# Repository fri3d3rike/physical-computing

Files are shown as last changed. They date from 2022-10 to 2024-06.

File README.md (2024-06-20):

# Physical Computing SS23 - Group 09

## Who we are

Friederike Mirza

We are Friederike Körte and Mirza Özokyay. Friederike is a Bachelor's student currently starting her advanced studies. Mirza is a Master's student and is familiar with electronics. 

## Topic

We are creating a telepresence system. Our device supports video calls by moving a tablet so that the participants of the call can see each other, even if the local participant moves to the left or right of the device. The device can follow a local participant's face or be manually controlled by a remote participant.

## Repository Structure

| Directory | Purpose |
|---|---|
| `Project` | Everything related to your project. |
| `Project/Concept` | Everything related to the concept or design of your project (ideas, drawings, mockups, mind maps, etc.). |
| `Project/Electronics` | Everything related to the electronics of your project (circuit diagrams, datasheets, etc.). |
| `Project/Mechanical` | Everything related to the mechanical aspect of your project (CAD, blueprints, datasheets, assembly, etc.). |
| `Project/Software` | The software aspect of your project. Most likely source code. |
| `Weekly Reports` | Weekly status updates as Markdown files. |
| `Weekly Reports/Figures` | Pictures or videos for your weekly reports. |

## Weekly Reports

Create a file called `PhysComp SS23 Group 09 Week <NN>.md` for every weekly assigment in `Weekly Reports`. For example: `PhysComp WS23 Group 02 Week 03.md`. Strictly follow this naming scheme and do not change it!
If you include pictures of videos, put them in `Weekly Reports/Figures`.

## Repository

### LFS

This template already comes with a pre-defined configuration for [Git LFS](https://git-lfs.github.com/). If you add any large binary files to your repository, update `.gitattributes` accordingly using `git lfs track`. For example if you add other video formats or CAD files that are binary, you need to track their file extension.

### .gitgnore

Please create according `.gitignore` files to ignore unnecessary files in the repository such as temporary files or build artifacts.

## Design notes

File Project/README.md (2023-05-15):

# PhysComp SS23 - Telepresence System

We are working on a device that holds a tablet and follows the user's face during a video call. The device can also be manually controlled by a remote participant. There are three operating modes: Stand (do nothing), Follow (the local participant's face) and Manual (controlled by remote user). The mode can be selected locally via a button on the device. The button is illuminated to show which mode is selected. Below the device, there is a sublte indirect light indicating the remote connection status (green/red). The device automatically powers on when a tablet is placed into the holder.

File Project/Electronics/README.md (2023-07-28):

# Electronics

The LEDs are connected to the Raspberry Pi GPIO pins with appropriate 220 Ohms resistors. The buttons are also connected to GPIO pins with configured pull-ups.

The connections of the ultrasonic sensors are interesting:

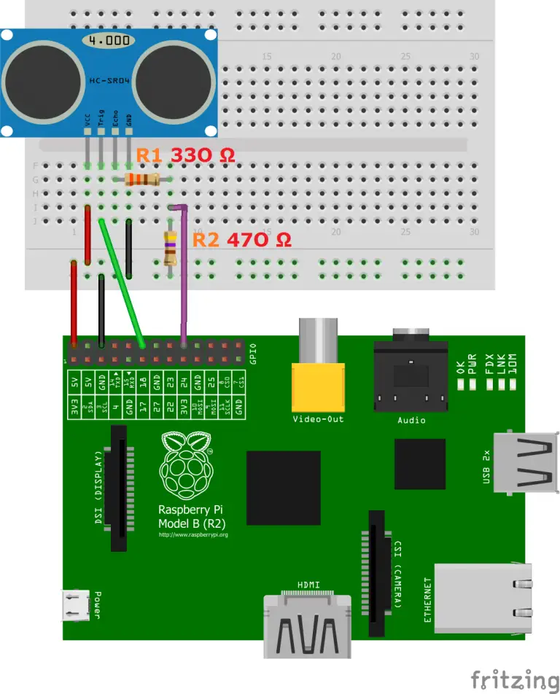
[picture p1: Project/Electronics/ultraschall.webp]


Source: https://tutorials-raspberrypi.de/entfernung-messen-mit-ultraschallsensor-hc-sr04/

We changed the 470 Ohms resistor to a 10k Ohms resistors which is said to work better.

The rest is described in the project reports, which is also where you can find our component list.

We wired everything on a breadboard.

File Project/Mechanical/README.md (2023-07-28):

# Mechanical

We create no sophisticated mechanical mechanism. The tablet angle can be chosen and of course the omni wheel platform enables the devices to drive around. Sketches, drawings and CAD files are in our concept folder.

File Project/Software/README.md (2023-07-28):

# Software

We wrote software to control the functionality of our prototype. There are two processors that we programmed:

* The Arduino Uno is for controlling the motors
* The Raspberry Pi is for handling user input and sending signals to the Arduino

## Arduino

The Arduino program is written in C and uses the Adafruit Motor Shield Library V2 to control the motors via the shield mounted onto the Arduino. It receives serial commands via USB from the Raspberry Pi. These commands contain (one byte each):

* Axis (forward/backward, left/right, rotate)
* Direction
* Motor speed

The program reads the serial commands in a loop and then sets the motor speeds accordingly. It also balances the speeds because one motor is weaker than the others. The progrma can be uploaded run from any Arduino compatible IDE.

https://github.com/adafruit/Adafruit_Motor_Shield_V2_Library

## Raspberry Pi

The Raspberry Pi is the brain of our prototype. It runs the latest Raspberry Pi OS Lite. Initially, we chose the Raspberry Pi because it is capable of image processing for the tracking mode. But since the actual tracking was not a top priority, we never actually implemented it. The main reason for that is that for some reason, the OpenCV library would not load the required modules. The Raspberry Pi handles all user input and sends commands to the Arduino. We simulated functionality that is not implemented via SSH. The Raspberry Pi does the following:

### A web server that serves our web UI

Since the Raspberry Pi has WiFi, we can connect it to a router and then access a small web server on it. The web server is realized in with Flask in Python. You can start it via ``start.sh``. It serves a static HTML page that has JavaScript code for GET requests when a button or key is pressed, found in ``static/index.html``. The GET requests are then handled by the Raspberry Pi. If the device is not in freeze mode, then the commands are forwarded to the Arduino to control the motors via serial commands. Since the hostname ``raspberrypi.local`` didn't work reliably (often quite delayed), we set up a static LAN address in the router.

Our code for the serial communication ``control.py`` was inspired by https://tutorials-raspberrypi.de/arduino-raspberry-pi-miteinander-kommunizieren-lassen/. We had to alter it to work with the current version of the library. 

### A Python script for our front panel

The ``frontpanel.py`` controls our front panel logic. It polls the buttons and sets the LEDs accordingly if a button is pressed. It also creates or removes the freeze file which indicates whether remote control has any effect. Since the "follow" mode is not implemented, it behaves the same as the "remote" mode, so we can simulate it.

### Some bash scripts for simulating functionality

The scripts ``red.sh``, ``green.sh`` and ``off.sh`` control the status LEDs below the device. Sine we have no actual login or connection system for the web UI, this simulates updating the status LEDs due to a user connecting/disconnecting.

### A python program for testing the ultrasonic sensors

The scripts ``ultra.py`` and ``ultra2.py`` poll from the left/right ultrasonic sensors. They show that the sensors are able to consistently detect edges. However, the data was never used because we did not want to risk our prototype breaking. Low motor speeds were not possible due to the weight, so the device was always a bit fast.

We took the electronic circuit and code from https://tutorials-raspberrypi.de/entfernung-messen-mit-ultraschallsensor-hc-sr04/ (modified).

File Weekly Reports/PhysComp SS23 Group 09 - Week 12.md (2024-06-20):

# PhysComp SS23 Group 09 - Week 12

## Progress Report

### What we achieved this week

We made our prototype ready for the evaluation. Here is a list of what we have accomplished:

* Added front panel button labels
* Created web interface for remote-controlled driving
* We tested a direct connection to a laptop using a self-hosted WLAN hotspot
* The connection was too unstable, so instead, we used a WLAN router for relaying the requests
* Tested the driving, found out that the batteries were too weak and replaced them
* Compensated a slow motor that caused the device to always turn by reducing the power of the other motors
* Added status LEDs below the device
* Added the on-off switch that is activated by placing the tablet into its slot
* Implemented logic for simulating the on-off switch (turns LEDs and functionality on/off)
* Implemented front panel logic (mode selection, corresponding LED is on, device ignores move commands if in freeze mode)
* Implemented a way to remote-control the status LEDs (red/green) below the device
* Glued on a power bank holder and the front panel

For photos, we refer to the evaluation.

We reached milestone 4 and part of milestone 5.

### What we could not achieve this week

We have not mounted the ultrasonic sensors and camera. This was not a problem because we had already planned to fake the edge detection and people recognition.

### What we plan to do for the coming week

* Mount the ultrasonic sensors and camera
* Incorporate some of the feedback from the evaluation: slower driving speed/acceleration, better web user interface
* Implement some way of detecting a connected remote user so that we don't have to fake it
* Maybe more improvements if there is time
* Reach milestone 5
* Send refund requests for the components we bought

## Evaluation Report

### Participants

We recruited our six participants from students of other courses. For that, we asked them personally or wrote them texts on WhatsApp. Students are a good representation of our target group because after the pandemic, they are very familiar with video calls and the problems that can arise. We recruited them between the 4th and 7th of July 2023.

All participants signed letters of consent and agreed on being recorded for our evaluation.

We had three groups of two participants each. One participant participated in the meeting in a room with Friederike using our device. The other participant went to a different room with Mirza.

### Functionality

The mode selection with LED feedback was actually working (except for the follow mode as mentioned before). In the freeze mode, no remote control is possible. Also, the remote-controlled driving was real since it is our core functionality.

We faked a lot of functionality. Since our web interface does not have a password-protected login system, remote users do not actually keep a connection to the device. They just send requests whenever they issue a drive command. This is why Mirza simulated the connection status LEDs (red/green/off) by remotely running commands on his laptop at the correct times. We also faked the automatic following mode since it was not ready. Mirza remote-controlled the device from his laptop in this mode. We did not find a safe way to fake the edge detection, but we made sure that the situation would not arise by starting the experiment with the device in the middle of the table. This was important to protect the device from damage. We also faked the on-off switch. The effects were basically the same as if it were actually implemented (LEDs turn on/off, the device does not respond to commands when off, the device always starts in freeze mode). The only difference was that the power to the Arduino and Raspberry Pi was kept on, allowing us to always be able to intervene if something were to go wrong. Also, this was much easier to implement instead of actually hooking up all the components to the switch.

### Instructions

We changed some of the tasks to be more focused on the core concept and capabilities of our device.

- **Task 0: Splitting up:**
  One user (local) stays with Friederike and the device. The other one (remote) goes to another room with Mirza.

- **Task 1: Device Setup:**
  The local user is provided with a tablet which is already in a Zoom call with Mirza's laptop next door. The remote participant can hear the instructions for the local participant through the call. The local participant is asked to turn on the device by placing the tablet in the holder.
  While doing that we observe the user's experience during the setup process, noting any difficulties or confusion encountered.

- **Task 2: Switch Device into the Remote Mode:**
  The user with the device is asked to switch from the default mode of the device into the Remote Mode. Then the user is asked to check the connection status of the device (simulation by Mirza).

- **Task 3: Remote Control:**
  The remote user is asked to move the device manually to look at Friederike who sits outside of his field of view next to the local participant.
  We observe if the device successfully moves and rotates toward Friederike. We check if it draws attention due to excessive noise, delays, or inaccurate movement.
  We observe if the remote user can interact with the user interface. We instruct them to also try out the control via the arrow keys instead of the buttons.

- **Task 4: Follow Mode Selection and Rotating Functionality:**
  The local user is asked to select a mode that causes the device to automatically follow a person in front of it. They are encouraged to move around so that the device has to rotate to keep them in the video.
  We observe if the device successfully rotates according to the user's input (simulated).

- **Task 5: Freeze Mode selection:**
  The users are instructed to set a mode that stops the device from moving and prevents remote control. We encourage the remote user to attempt to move the device.
  We observe if the mode selection is intuitive.

- **Task 6: Turn off the device:**
  The local user is asked to turn off the device. If they do not know how, we give them the hint to take away the tablet.

### Observations

We made many interesting observations when watching the participants interact with our prototype.

* Although we explained the concept of our speak-aloud study, the participants generally kept quiet. We had to ask them to comment on their observations.
* If the tablet is in a protective case, some force is needed to push it into its place and activate the power switch. The first participant was not sure if they should apply so much force. For later trials, we removed the tablet case, making the process much simpler.
* One local user placed the tablet in portrait orientation instead of landscape orientation. We instructed them to change to landscape so that the tablet would not fall over.
* During one trial, a wheel came off. We were able to quickly stick it back onto its axle and continue the experiment.
* One participant acted as if they were afraid that the device could drive off the table.
* To one participant, it was not clear that the front panel LEDs are pushable buttons.
* During movement in one trial, the tablet briefly came off the switch, causing the device to quickly turn "off" and reset to the freeze mode. This was very unexpected and confused all of us.
* Some local participants did not notice the status LEDs below the device. We believe that this is because especially the red LEDs are not bright enough.
* In our web interface, users often did not use the "turn left"/"turn right" buttons, but instead only the "left" and "right" buttons. We should probably swap their places to make the more important rotation buttons more prominent. Likewise, the left/right arrow keys should control the rotation and only need "shift" for driving sideways.

Here are some pictures of us doing the evaluation with the participants:

At the beginning:

Evaluation

Our participants filling out the survey (Google Forms):

Evaluation

A remote participant in the other room:

Evaluation

One study participant while testing the rotating functionality:

<video src="Figures/evaluation.mp4" controls width="100%"></video>

### Online Surveys

Both participants answered the same surveys. Some questions were more suitable for either the present or remote participant, but we always let both answer all questions from their perspectives. We evaluate them separately if appropriate.

#### Pre-Test Survey

Pre-Test Survey
Pre-Test Survey
Pre-Test Survey
Pre-Test Survey
Pre-Test Survey
Pre-Test Survey
Pre-Test Survey
Pre-Test Survey
Pre-Test Survey

Participants generally understand the idea of a telepresence device (some needed a short explanation during the survey). They saw a need for such devices. Many were not very familiar with telepresence devices, though. Also, more than half of our participants were not confident with controlling a physical device via web-based interface.

#### Post-Test Survey

Post-Test Survey
Post-Test Survey
Post-Test Survey

Was the mode selection intuitive?  
$\Rightarrow$  all participants answered with highly intuitive

How intuitive and user-friendly did you find the mobile app or web-based interface for controlling the device?  
$\Rightarrow$  all participants using the interface answered with highly intuitive

Post-Test Survey
Post-Test Survey
Post-Test Survey
Post-Test Survey
Post-Test Survey

Our participants found the setup easy. They liked the (simulated) automatic tracking. All participants agreed on the mode selection being intuitive. They all found the web interface to be highly intuitive. Participants criticized that the device was a bit unstable/unsecure. Participants were mostly comfortable during the session, but this did not apply to all.

They gave us helpful feedback regarding a free space for the device and suitable ground and also pointed out that there would be fewer problems if the device only rotates. This is nothing really new to us, but it shows us that they understood the concept very well.

Our participants suggested refining the movement behavior (less stuttering and noisy). They would like obstacle/edge detection and a more secure tablet holder that also secures the tablet on the sides.

All except for one would use the device. One participant thinks that the device is overkill for small meetings.

### Post-Test Interview

After the experiment and the post-test survey, we briefly interviewed our participants together in person. We chose to do it this way to make it as comfortable as possible for them. We asked them especially for anything that they would like to comment on but did not write into the survey. We encouraged them to tell us everything about their experience during our study that came to their minds. Here are their comments:

* The device is quite loud
* The device might fall off the table
* The tablet camera angle is not ideal for large tables
* A way to remotely control the tablet angle vertically would help
* The device moves stuttering 
* Unexpected movement scared someone
* The device is probably very good for presenters like professors
* A user placed the tablet in portrait orientation only because it already was this way on the table
* When asked, nobody noticed the possibility to manually change the vertical tablet angle
* A way to secure the tablet on the sides would be good
* Unsure what happens if there are many people in front of the device in automatic following mode
* The device is quite big and does not fit in a small bag, so it is not very portable
* Sometimes, the automatic tracking is too slow (was simulated to be as realistic as possible)
* Participants generally liked our front panel, the button labels, colors, and feedback due to the LEDs lighting up
* At the beginning, it was not clear what the status LEDs below the device communicate (until they turned green exactly when the remote user "connected")

After the study, participants received a Kinder Bueno as compensation for their time.

### Conclusions

We are very happy that our participants liked our core concept. Participants found interaction with parts of the device that were in our main physical concept very intuitive, specifically powering the device on/off by placing/taking the tablet and the mode selection. This is especially good when considering that in the pre-test survey, many participants were not familiar with telepresence devices.

We cannot make fundamental changes to our concept so shortly before the final presentation. For example, we cannot implement remote control for the vertical tablet angle. However, there are small things that we can polish:

* We can reduce the motor speed to make the device less scary, loud, and abrupt
* We can make the acceleration gradual to make movements smoother
* We can swap the "turn" and sideways (left/right) buttons of our web interface
* We can add ultrasonic sensors for edge detection (or at least the simulation of it for our presentation)

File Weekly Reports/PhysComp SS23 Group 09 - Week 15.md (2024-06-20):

# PhysComp SS23 Group 09 - Week 15 - Final Report

## What we achieved in Week 14

As planned in our previous report, we added a third ultrasonic sensor in the back. This way, there is no risk of driving off an edge when going backward. There is no ultrasonic sensor in the front because we found nowhere to put it, it would look stupid and it also is not really necessary since you can see where you are going when driving forward.

Ultrasonic Sensor Back

The ultrasonic sensors on the sides are wired up and working. However, we don't trust them enough to test the edge detection when actually driving. Due to the weight of our device, the motors require a minimum power that makes it go quite fast. The measurements prove that it is indeed possible to detect an edge from the readings in theory.

Ultrasonic Sensor Console

Code by https://tutorials-raspberrypi.de/entfernung-messen-mit-ultraschallsensor-hc-sr04/

We also asked other students whether we should encase the ultrasonic sensors. The voted for yes with 2:1 votes. Our prototype now looks more polished:

Ultrasonic Sensor Exposed
Ultrasonic Sensor Encased

We decided that it isn't worth the effort to do more programming or even try to implement more functionality. Proper tracking would be nice, but also very time-consuming to implement. We fixed a few bugs with the UI, though. In its current state, with a little bit of magic, our prototype can exactly showcase our whole vision for the telepresence system. This is why we call it complete and milestone 5 is reached (almost on time).

### We also found a missing photo of our drawing for the wooden parts

Wood Drawing

We gave this drawing to the scientific engineering services. They cut our wood parts.

### Updated READMEs

We updated the READMEs of all directories in the Project directory to include useful information.

## Concluding report

Our prototype is a Telepresence Device designed for users attending hybrid meetings with their laptop or tablet. Its goal is to achieve a more active engagement in remote meetings.

### What works:
- Turning on the device with a switch by placing the tablet inside the holder
- Selecting between 3 different modes to change between different functionalities of the device
- Giving the user feedback about which mode is currently selected by the according LED light, inside the button that was pressed, being turned on
- The device has red and green status LEDs underneath
- The device does not move when in mode: freeze
- The device moves in response to the remote participant pressing the keyboard or interacting with the graphical interface (and that pretty well and accurately)
- There is a graphical interface with which the remote participant can control the device
- The device has two out of three wired and working ultrasonic sensors to detect edges

### What plans changed:
- We found a camera for the Raspberry Pi and then changed the concept to have a more independent device which does not also have to access the connected tablet/smartphone's camera
- We didn't fully implement the edge detection because we already planned in the beginning that that is not our main focus and we would only do it in the end, if we have enough time (optional goal)

### What doesn't work:
- The tracking functionality (the OpenCV library caused problems)
- The feedback whether there is a connection to a remote (red/green status LEDs) user is not automatic yet (there is no login system)
- The edge detection: The ultrasonic sensors on the sides are wired up and working, only the one on the back is not wired. They do not force the device to stop yet if an edge is detected. We did not implement it because we would not risk our device being damaged anyway.

### What could work if...:
- All the things that are not completely functional yet could be improved to work if we would have had more time
- The ultrasonic sensors, as well as the feedback LEDs, are connected to the Raspberry Pi, they just need to be implemented in the code to fully work (use the sensor readings which we already have, create some kind of session in JavaScript for the LEDs)
- The tracking would be a little bit more effort than the other things, but the camera is already connected and works and communicates with the Pi, so we would need to get the library working. Then just send the appropriate motor commands if a face is detected far enough off-center.
- If the device were a bit lighter, then the motors could go slower (yes, it's counter-intuitive). After the evaluation, we reduced the speed, but an even slower speed might be desirable.

### Demonstration

You can access our final presentation as [PDF](../Project/Concept/PhysComp_SS23_Final_Presentation.pdf) and [PPTX](../Project/Concept/PhysComp_SS23_Group_09_Final_Presentation.pptx) (with some videos included).

Here are all videos to show the prototype in action (please ignore the beeping sounds of our neighbor's prototype):

##### Setup 


##### Mode Selection


##### Remote Modus: UseCase 1


##### Tracking Modus: UseCase 2


##### Edge Detection  


##### Device Rotating  


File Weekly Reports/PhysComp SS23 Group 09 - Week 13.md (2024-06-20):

# PhysComp SS23 Group 09 - Week 13

## Progress Report

### What we achieved this week

We implemented all of the missing hardware features and improved our software.

* Mounted the camera module, connected it to the Pi
* Added ultrasonic sensors, they are wired up and give measurements
* Added cardboard brackets that hold the tablet in place
* Changed the resistors for our red status LEDs from 220 Ohms to 120 Ohms to make them brighter
* Improved the web UI: swapped the buttons/keys for turning and strafing

#### New web UI
The web UI

#### Final state of the electronics underneath the hood
Electronics
Electronics

#### Final state of the prototype
Final Prototype
Final Prototype with Tablet

<video src="Figures/prototype_moving.mp4" controls width="100%"></video>

### What we could not achieve this week

We haven't added four ultrasonic sensors, only two.

### What we plan to do for the coming week

* Maybe add another two ultrasonic sensors, if we can find a way to mount them. Then all movement directions are safe.
* Maybe implement an easier way of simulating the webUI authentication and connection for the status LEDs
* Prepare and exercise our presentation

## Evaluation Report

There was nothing new to evaluate.

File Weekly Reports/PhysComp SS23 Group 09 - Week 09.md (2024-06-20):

# PhysComp SS23 Group 09 - Week 09

## Progress Report

### What we achieved this week

#### Arduino Motor Test
We decided that it is easiest to use the motor shield with our Arduino since it is designed to work with it. We still need the Raspberry Pi for the image processing, though. So our project will use both an Arduino and a Raspberry Pi.

We mounted the motor shield onto the Arduino. This was easy, because we had desoldered many unnecessary wires a few weeks prior. A problem was that a poorly soldered pin had a connection issue, but with some pushing and pulling, it is solved for now. We might want to re-solder the pin if the problem arises again. We then ran the example code for the motor shield as a test.

Motor Test

#### Raspberry Pi
In order to get the Raspberry Pi working, we borrowed an SD reader from another group (we expected the Uni to have a microSD-SD adapter, but there was none to be found). We then installed a Raspbian Lite image onto our microSD card and configured it to connect to my laptop via WLAN. After a bit of troubleshooting, everything worked fine. We then tried connecting the Raspberry Pi to the Arduino via USB, but there seems to be some issue with the serial port configuration on the Pi. We have to look into that next week.

We also decided to use the Raspberry Pi camera module which we found in a box in the HCI lab. This way, our system can operate independently from the tablet, making it much simpler and hopefully more robust. We have to figure out where to mount the camera.

#### Building the Physical Parts
We created plans with proper measurements for the base that connects the tablet holder to the omni wheel platform. Unfortunately, we forgot to take pictures. We gave the plans and some wood scrap to the engineering services and hope to receive our parts in the next few weeks.

We also 3D printed our front panel. It came out exactly as expected.

Front Panel Printed
Front Panel Printed

### What we could not achieve this week

* Construction plan for the top part (including spot for the Raspberry Pi camera)
* Plan for mounting the ultrasonic sensor
* Raspberry Pi to Arduino connection

### What we plan to do for the coming week

* Plan the top part, camera, and ultrasonic sensor placement (reach Milestone 1)
* Hopefully receive parts from the engineering services, work on the top part (toward Milestone 2)
* Connect Raspberry Pi to Arduino for motor controls, test the camera (toward Milestone 3)

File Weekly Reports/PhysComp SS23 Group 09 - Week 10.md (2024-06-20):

# PhysComp SS23 Group 09 - Week 10

## Progress Report

### What we achieved this week
Friederike could not attend the lecture due to the overlap with another course, but worked from home. 
We got the wood parts we had ordered at the wood workshop and prepared them for the next milestone.

Wood Parts
Wood Component

We also managed to get the connection from the Raspberry Pi to the Arduino to work. We had to replace the camera cable to connect the camera to the Pi. For that, we borrowed a high-quality camera module with a compatible cable. We do not use the high-quality camera module, because it is very big and also requires a big lens which we do not have. With the new cable, our camera works, but for some reason, the OpenCV library does not load certain modules on the Pi. We might implement the face tracking in a Wizard of Oz fashion.

The first photo taken with the Raspberry Pi camera:

First Pi Cam Image

### What we could not achieve this week

The OpenCV library does not load the modules required for the face tracking. Also, the LEDs still have to be connected and the front panel must be assembled. The LED and motor controls have to be programmed.

### What we plan to do for the coming week

* Reach milestone 3
* Assemble everything (top part of the device, front panel, LEDs, camera, on-off switch)
* Set up the remote control

## Evaluation Plan:

### Usability Test Plan: Telepresence Device for Hybrid Meetings

### Introduction:
The purpose of this usability test is to evaluate the functionality, ease of use, and overall user experience of the telepresence device designed for users attending hybrid meetings. The target group for this test is people who actively engage in remote meetings and need a seamless and immersive experience. The test will focus on assessing the device's rotation capabilities, tablet/phone holding mechanism, setup process, adaptability to different meeting spaces, and user interface.

### Test Objectives:

- Evaluate the ease of setup and use of the telepresence device (turning it on).
- Evaluate the ease and understandability of the mode selection.
- Assess the functionality of the device's ability to rotate and its ability to follow a person's face.
- Determine the effectiveness and security of the tablet/phone holder.
- Test the adaptability of the device to different meeting spaces.
- Evaluate the intuitiveness and user-friendliness of the web-based interface of the remote participant.
- Gather feedback on overall user experience and identify areas for improvement.

### Number of Test Users:
To test the device we need at least pairs of two. So that one person can be with the physical product while the other person interacts remotely (ideally from another room). If possible, it is preferable to have even multiple users interacting simultaneously during the test to simulate realistic meeting scenarios and assess any potential issues with concurrent usage.

### Target Group:
Users who regularly participate in hybrid meetings with their tablet/pc/smartphone etc. and require remote participation. The participants should have experience with remote collaboration tools and video conferencing software like Zoom, Teams, etc. Students are an ideal test group since they have experienced lots of video calls during the pandemic. They know the problems that they have had and can understand how they would benefit from our device.

### Test Tasks and Scenarios:

- **Task 1: Device Setup:**  
  The user with the device is asked to unpack and set up the telepresence device on a table or desk. The user is provided with a tablet and asked to turn on the device by placing the tablet in the holder.
  While doing that we observe the user's experience during the setup process, noting any difficulties or confusion encountered.

- **Task 2: User Interface:**  
  The users are provided with a web-based interface for controlling and connecting the device.
  Then both of the users are instructed to connect to the device using the interface.
  We observe the user's interactions and note any challenges or areas of confusion. Do the two groups get the device to connect without problems?

- **Task 3: Remote Control:**  
  The remote user who is not present in the room with the device is asked to rotate the device manually to look at different participants in the other room.
  We observe if the device successfully rotates to track the user's face and adjusts its position accordingly. Drawing attention to excessive noise, delays, or inaccurate tracking.

- **Task 4: Mode selection:**  
  The users are instructed to set the mode to the freeze mode to prevent remote control. Then they are asked to select a mode that causes the device to automatically follow a person in front of it.

- **Task 5: Rotating Functionality:**  
  We instruct the user with the device to move around in the room while the device is set to follow their movements.
  We observe if the device successfully rotates according to the user's input and if the control via the keyboard was intuitive.

### Test Procedure:

1. **Introduction and Pre-Test Survey:**  
   Providing an overview of the test objectives and procedures to the participants. Asking for permission to collect the data and informing them what the data is needed for. 
   Collecting background information about the participants, including their experience with hybrid meetings and remote collaboration tools.

2. **Demonstration:**  
   We present a brief demonstration of the telepresence device's features and capabilities to familiarize participants with its functionality.

3. **Test Execution:**  
   We encourage the participants to think aloud, express their thoughts, and verbalize their experiences as they use the device.
   Assigning the tasks to the participant and taking notes on participants' interactions, difficulties, and feedback.

4. **Post-Test Survey:**  
   Post-test questionnaire to gather additional feedback and subjective impressions from the participants.
   Participants can ask questions, share their overall impressions, and provide any additional comments.

### Additional evaluation technique: Survey 

#### Pre-Test Survey: 

1. How frequently do you participate in hybrid meetings or remote collaborations? - [never, monthly, weekly, daily]
2. Which tools or devices do you currently use for remote meetings? Please rate their effectiveness on a scale of 1 to 5. [1 - Not effective, 5 - Highly effective]
3. On a scale of 1 to 5, how challenging do you find it to actively engage in remote meetings? [1 - Not challenging, 5 - Highly challenging]
4. How familiar are you with telepresence devices or similar technologies? Please rate your familiarity on a scale of 1 to 5. [1 - Not familiar, 5 - Very familiar]
5. On a scale of 1 to 5, how important is it for you to actively engage and contribute during remote meetings? [1 - Not important, 5 - Very important]
6. Have you used any rotating or tracking devices before? Please rate your experience with them on a scale of 1 to 5. [1 - Negative experience, 5 - Positive experience]
7. How confident are you with using mobile apps or web-based interfaces for controlling physical devices? Please rate your level of confidence on a scale of 1 to 5. [1 - Not confident, 5 - Very confident]
8. What features or functionalities do you expect from a telepresence device for hybrid meetings?

#### Post-Test Survey:

On a scale of 1 to 5...

1. How would you rate the ease of setup and initial configuration of the telepresence device? [1 - Very difficult, 5 - Very easy]
2. Did you find the rotation functionality of the device effective in tracking your movements? [1 - Not effective, 5 - Highly effective]
3. Was the mode selection intuitive? [1 - Not intuitive, 5 - Very intuitive]
4. Did you feel that the telepresence device enhanced your ability to actively engage in the hybrid meeting? [1 - No impact, 5 - Significant impact]
5. On a scale of 1 to 5, how intuitive and user-friendly did you find the mobile app or web-based interface for controlling the device? [1 - Not intuitive, 5 - Highly intuitive]
6. How secure and stable did you find the tablet/phone holder for different sizes of devices?  [1 - Not stable, 5 - Highly stable]
7. How comfortable did you feel using the telepresence device during the test session? [1 - Not comfortable, 5 - Very comfortable]
8. Were there any challenges or difficulties you encountered when adapting the device to different meeting spaces?
9. What suggestions do you have for improving the overall usability and functionality of the telepresence device?
10. Based on your experience, would you consider using the telepresence device for your future hybrid meetings? Why or why not?

### What we hope to learn 

* What are common issues, patterns, and areas of improvement?
* Do people understand how to use the device (setup, mode selection)?
* What could be specified more clearly?
* How would we create a manual for the device?
* Are there any risks when using the device?

### What functionality can you test, what can you fake (Wizard of Oz)?

The changes in LED lights in response to button presses (mode selection, on/off switch, connectivity light) are hard to fake but easy to actually implement. We might have to simulate the device detecting edges via the ultrasonic sensors. Also, we might have to fake the mode of following a person if we cannot get the OpenCV library to work on the Pi.

Gif

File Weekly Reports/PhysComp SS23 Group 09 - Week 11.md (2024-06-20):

# PhysComp SS23 Group 09 - Week 11

## Progress Report

### What we achieved this week

Soldering
Soldering

We worked on Milestone 4. We soldered the buttons and connected them to the front panel. 

Frontpanel

We assembled all the inner parts and started programming.

Inner Parts
All Together

In theory, the functions for moving in different directions are now ready, but we have not tested them.

We also created the labels for the front panel:

Front Panel Labels

We created a letter of consent: [consentletter.pdf](/Project/Evaluation/consentletter.pdf)

We also created two Google Forms for the pre and post test surveys and a consent form for our Evaluation Plan.

### Concept Change

Since we are using the Raspberry Pi camera for tracking participants, we no longer rely on a connection to the tablet. This makes our device more robust and makes the setup even easier. Now, the status LEDs no longer display the connection to the tablet, but:
- If the mode is freeze: whether the device is on
- If the mode is follow: whether the device is detecting a participant to follow
- If the mode is remote: whether a remote user is connected

### What we could not achieve this week

* Find people for the evaluation
* Milestone 4

### What we plan to do for the coming week

Finish milestone 4 and start with 5:
* Front panel button labels
* Test driving
* Create web-interface for movement control
* Add status LEDs below the device
* Add on/off switch
* Write logic for controlling LEDs and on/off switch
* Assemble the rest (front panel, power bank, tablet holder)
* Low priority: Mount ultrasonic sensors and camera (not used for evaluation)

Find people for the evaluation of our prototype and evaluate.

## Evaluation Plan Refinement

For the Evaluation Plan, most remained the same as you can find in the last report of week 10. We added the handout of a consent form in the introduction step of the procedure and also reworked the test tasks a little bit to be more specific.

### Introduction:
We greet the participant, introduce ourselves, and briefly describe our project and the purpose of this study:
The purpose of this usability test is to evaluate the functionality, ease of use, and overall user experience of the telepresence device designed for users attending hybrid meetings as part of the Physical Computing Course SS23 at the University of Konstanz. The target group for this test is people who actively engage in remote meetings and need a seamless and immersive experience. The test will focus on assessing the device's rotation capabilities, tablet/phone holding mechanism, setup process, adaptability to different meeting spaces, and user interface.  
Then we give the participant a consent form to sign and introduce them to the tasks. 

### Test Tasks and Scenarios:

- **Task 1: Device Setup:**   
  The user with the device is asked to unpack and set up the telepresence device on a table or desk. The user is provided with a tablet and asked to turn on the device by placing the tablet in the holder. Then both of the users are instructed to connect to the device.
  While doing that we observe the user's experience during the setup process, noting any difficulties or confusion encountered.

- **Task 2: Switch device into the Remote Mode:**  
  The user with the device is asked to switch from the default mode of the device into the Remote Mode. Then the user is asked to check the connection status of the device.

- **Task 3: Start Video Call:**  
  The participants are asked to start a video call.
  We observe how confident the user is with the use of their laptop. 

- **Task 4: User Interface:**  
  The users are provided with a web-based interface for controlling the device.
  We observe the user's interactions and note any challenges or areas of confusion. Do the two groups get the device connected without problems?

- **Task 5: Remote Control:**  
  The remote user who is not present in the room with the device is asked to rotate the device manually to look at different participants/directions in the other room.
  We observe if the device successfully rotates to track the user's face and adjusts its position accordingly, drawing attention to excessive noise, delays, or inaccurate tracking.

- **Task 6: Follow Mode selection and Rotating Functionality:**  
  The users are asked to select a mode that causes the device to automatically follow a person in front of it. They are encouraged to move around.
  We observe if the device successfully rotates according to the user's input and if the control via the keyboard was intuitive. 

- **Task 7: Freeze Mode selection:**  
  The users are instructed to set the mode that stops the device from moving and prevents remote control.

- **Task 8: Turn off the device:**  
  The user is asked to turn off the device by taking away the tablet.

## Milestone Review

No milestone is overdue. We would have liked more progress on milestone 4. We had to set the deadline quite late, but we need parts of the functionality for the evaluation. We will have to figure out how to handle this in the next session. We decided that it does not make sense to add another milestone specifically for the evaluation because it is hard to predict our progress.

1. Concept complete (DONE)
   - Features clearly described
   - Parts, sizes, etc. planned out
   - Mandatory and optional goals

2. All parts prepared (received, cut, printed) (DONE)
   - Cutting
   - Printing
   - Ordering

3. Electronic components tested (DONE)
   - Components tested individually
   - Certain features tested: LEDs, buttons, camera, motors

4. Prototype assembled - Deadline 19.07.2023 (WIP)
   - GOAL: Prototype assembled, components connected and tested
   - TODO: Test driving code (weight/torque considerations)
   - TODO: Properly mount ultrasonic sensors and camera
   - TODO: Install LEDs under the device
   - TODO: Mount front panel
   - TODO: Mount power bank
   - TODO: Install on/off switch
   - TODO: Finish tablet holder

5. Prototype functional - Deadline 26.07.2023
   - GOAL: Programming complete
   - TODO: On/off switch shows an effect
   - TODO: Mode selection works
   - TODO: Status LEDs work
   - TODO: Remote control works
   - OPTIONAL: Face tracking and automatic rotation
   - OPTIONAL: Edge detection

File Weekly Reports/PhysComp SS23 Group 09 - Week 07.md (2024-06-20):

# PhysComp SS23 Group 09 - Week 07

## 3D Printing

We modeled a cup with our initials in Autodesk Fusion. The STEP file is in our Concept folder.

CupCAD

We are planning on using 3D printing for our front panel and possibly other parts like the supports that connect the wheel platform with the top board.

## Progress Report

### Milestones

We came up with five milestones. Small changes are possible even after the concept has been completed.

1. Concept complete
   - Features clearly described
   - Parts, sizes, etc. planned out
   - Mandatory and optional goals

2. All parts prepared (received, cut, printed)
   - Cutting
   - Printing
   - Ordering

3. Electronic components tested
   - Components tested individually
   - Certain features tested

4. Prototype assembled
   - Prototype assembled, but not fully programmed

5. Prototype functional
   - Programming complete
   - Connection with tablet established
   - Things that could not be implemented must be faked (edge detection, automatic connection)

## Concept changes

We thought about the placement of the ultrasonic sensors. They are now in our sketches.

SketchPrototypeWithSensor

### What we achieved this week

The ordered components have arrived. We created a milestone plan.

We also consulted the scientific engineering services for available transistors. We have to check if there are suitable parts for us.

Transistors

### What we could not achieve this week

We have not fully finished the concept because Friederike could not attend the lecture.

### What we plan to do for the coming week

We will finish the concept and start preparing all parts.

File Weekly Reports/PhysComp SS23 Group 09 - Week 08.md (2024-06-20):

# PhysComp SS23 Group 09 - Week 08

## Soldering Exercise
Report on your soldering exercises (pictures/videos and text). What was your experience, what *challenges* did you face, what was the *outcome*?

### Challenges  

The main challenge was to get the solder heated up at the right position, because not all sides of the soldering iron were hot. So it sometimes took a little patience or a new position of the soldering iron until the wire could be soldered. We used the helping hand and a flux pen, that helped the solder flow cleanly onto the parts we were soldering.
Another challenge was to reach the position between all the wires, but the helping hand and cutting and bending the finished wires away helped a lot and all in all we are satisfied with the result.
It took us some time to check the polarity of the components, but the manual and prints on the PCB told us everything we needed.

Here is a photo of us soldering: 

MirzaSoldering

### Outcomes 
Our outcome is a very nice little light organ that lights up when the microphone detects a sound.

<table>
<tr>
<td>Outcome1</td>
<td>Outcome2</td>
</tr>
</table>

<video src="Figures/videoLEDOrgel.mp4" controls width="100%"></video>

## Weekly Progress Report

### What we achieved this week

Since the most important components have arrived, we wanted to start testing them to see if we need to order anything else. The power bank and rolling lever switches work fine. The LED buttons, however, posed a little challenge. There was no data sheet and the Amazon website only stated something like "12V LEDs, switch 230V". Unfortunately, we found no other sellers that offered similar buttons with a more trustworthy description. We assumed the buttons contain resistors to make them work with 12V. Just to be sure, we decided to test an orange button (a color we would not need later on) with 3.3V and quickly burned out the LED. We realized that the buttons do in fact not contain any resistors. We then soldered some of the leftover leads from the soldering exercise to a new button and tested it on a breadboard with an appropriate 470 Ohms resistor. It worked just fine. This is nice because now we know that we won't need transistors to power the LED buttons.

Button Legs

We also designed the CAD model for our front cover after measuring the buttons. Since the buttons are quite small, the panel has to be only 2 mm thin. We added ridges for structural stability. It is located in our concept folder and we would be happy to have it printed as soon as possible to see if everything fits.

<table>
<tr>
<td width="35%">Button Measure</td>
<td>Front Panel</td>
</tr>
</table>

### What we could not achieve this week

We have not reached our first milestone. We still have to create exact sketches or CAD models for the remaining structure of our device.

### What we plan to do for the next session (the coming week is a holiday)

* Decide which other parts must be 3D printed
* Create accurate sketches or CAD models
* Acquire the materials (cardboard, plastic)

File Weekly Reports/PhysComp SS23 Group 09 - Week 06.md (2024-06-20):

# PhysComp SS23 Group 09 - Week 06

## Feedback Report

### Concept Presentation

_Briefly summarize the feedback and comments you received on your concept presentation. List the most critical points (aim for at least 3)._

- Consider renaming the labels of the three front buttons on the device, because they might not be intuitive 
- Is the placement of the tablet on the device final? Maybe also consider the middle instead of the front for a better balance.
- How is the person/movement tracking implemented?

_Describe how you could address these (you’re welcome to discuss this hypothetically to achieve your vision, if you don’t plan to actually realize it in your prototype)._

We thought about different names:
- off, disabled, still, hold, motionless, pause, freeze
- manual, remote
- automatic, track, follow

We then decided for two variants:
- Technical: disabled, auto, manual  
- Descriptive: freeze, follow, remote

We favor the descriptive terms because they are better understood by non-expert users.

The tracking is implemented solely with the tablet's camera. We do not use audio signals because we think that it is hard to locate their origin and to distinguish speaking from background noise. Also, we want to avoid the device moving around all the time because someone speaks.

ButtonsSketch

### Peer Evaluation

_Briefly report on how you evaluated your own prototype/concept/storyboard with your partner group. (Did you discuss the storyboard? Did you play out a scenario in Wizard of Oz-style?) What was your experience?_

We used the storyboards to explain the possible functions and applications of our device and mostly worked with the paper prototype to discuss improvements. Therefore, it was really useful to already have the low fidelity prototype to take it and imagine the final product. Not much of a simulation was needed because our features and use case are quite clear.

_What main feedback did you get here?_

### Feedback  
1. A way to change the angle of the smartphone/tablet would be helpful
2. Edge detection/feedback that the device is close to falling off the table is needed
3. Make the tablet more secured when it is on the device 
4. What happens when there is more than one person in front of the device (_follow mode_)?
5. Using a counterweight for a better balance 
6. Colors of the buttons?
7. A smartphone remote (app) would be cool

_What group did you partner up with for the prototype evaluation? Very briefly describe their project concept and summarize the most critical feedback points you gave them._

Other Group

We partnered up with group 7. Their project is the Aurora Analog Timer. It's a time management tool for presentations consisting of two components. There is the main component, a timer with visual and sound feedback. The second component is a small remote with haptic feedback. You can also set checkpoints when you want to be reminded how much time you have left.

When giving our feedback we mostly had questions to the other team and ideas of what should also be considered. For example, does the timer stop making a noise when the remote is placed back into the station on top of the main component or only if the stop button is pressed? What is the remote for? Could it maybe also be a laser pointer? Is there also a start and stop button on the remote? How is the checkpoint set? Can there be more than one checkpoint? Is there any feedback once the checkpoint is set? How can you add more time to the timer once it is already running? Is it possible to set more than 1h because that corresponds to one turn of the clock hand to set the time? Is there a maximum number of checkpoints? Is there a maximum time that can be set? Maybe it is smart to label the inner circle with 15, 30, and 45 minutes to indicate the time intervals. 

## Progress Report

_Update your concept/storyboard according to the feedback you received after your presentation and in the peer evaluation (you will need these illustrations again when you present your final project, so it’s worth the effort). Make sure you briefly report on these changes (in words/pictures)._

### Decisions regarding the Feedback we received

We think that the tablet won't fall off, but we will have to test this in practice once the motors are functional. We might limit the motor speed for slower acceleration/deceleration. We will have to test the final balance and maybe add a counterweight. We like our design with the tablet being right at the front of the device, minimizing the distance to the local participants.

The tracking is implemented solely with the tablet's camera. For simplicity, we decided that the device should not follow anyone if there are multiple people recognized in front of it. This way, the behavior should be easy to understand and predictable. 

In order to prevent the device from falling off edges, we might add ultrasonic sensors.

We have not fully decided on the button colors. In theory, the modes are equally relevant. Also, there are no intuitive colors for these modes. However, since the freeze mode should only be used temporarily (otherwise, you could just use a tablet stand), it might get a different color. In order to prevent a mapping like red = bad, the colors could be blue and white.

Regarding the smartphone remote, we are not sure if it is out of the scope of our project. We will keep it as an optional goal.

### What we achieved this week

We presented our concept to the class, got and gave feedback, and then worked on improving our paper prototype and implemented the given feedback.  

We added something to change the angle of the tablet.  

Prototype angles

And we renamed the three buttons and added descriptive icons. 

Buttons updated

Prototype updated

Also, we ordered the missing components so that we can try them next week and have time to order something else if needed. We ordered the following components from Amazon:

* Mikroschalter Rollenhebel 10 St. 4.99€
* LED Tastschalter 10 St. 7.99€
* Power Bank 20000mAh 21.95€

Links:
* [Mikroschalter Rollenhebel](https://www.amazon.de/dp/B07F9QKTQQ)
* [LED Tastschalter](https://www.amazon.de/dp/B09QQJWTL5)
* [Power Bank 20000mAh](https://www.amazon.de/dp/B08G96F4ZF)

### What we could not achieve this week

Nothing :)

### What we plan to do for the coming week

* Test the ordered components
* Create precise plans for building the device
* Think about parts that need to be 3D printed
* CAD modeling
* Maybe start soldering and building

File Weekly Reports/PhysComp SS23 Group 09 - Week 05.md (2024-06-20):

# PhysComp SS23 Group 09 - Week 05

## Progress Report

### What we achieved this week

OmniBase  

We created another paper prototype. This time we used the Omni Wheel Base from class as the main component and built the smartphone holder construction on top of it. That didn't change a lot about the concept but mainly the look of our device. Our new prototype also includes the 3 buttons we decided to add. They show the current mode with a small LED light inside the button. 

Prototype2

PrototypeTablet

We thought about where to position the buttons.  

**Option 1**:  on the front, below the tablet/smartphone.  

Prototype2Sketch

**Option 2**:  somewhere on the side, not directly visible when looking at the front/ tablet.   

Prototype2SketchButtonsOnSide

We decided to go with Option 1 because the user then can always immediately see which mode is active due to the light inside the button. And it's easier to locate the buttons because they are in direct field of view.

We prepared our concept for the presentations in front of the class this week.  
 
### What we could not achieve this week

The buttons are only indicated and not yet really pressable in the prototype.

### What we plan to do for the coming week

Order the missing components and start building the real prototype.

### Component List

#### To order
* USB power bank (https://www.amazon.de/gp/product/B08G96F4ZF)
* Three Push-buttons with integrated white LEDs (https://www.amazon.de/gp/product/B09QQJWTL5)
* A suitable switch that requires little force so that it can act as the main power switch (https://www.amazon.de/gp/product/B07F9QKTQQ)

#### Available
* Raspberry Pi 3
* MicroSD card for the RPi
* Batteries (AA and 9V)
* Omni Wheel Platform with motor controller
* Three red and three green LEDs
* Jumper wires
* Breadboard
* Resistors
* Small wood or plastic pieces for the case and tablet holder
* Maybe 3D-printed parts that fit and look better

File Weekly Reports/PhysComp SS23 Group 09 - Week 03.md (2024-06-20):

# PhysComp SS23 Group 09 - Week 03

## Progress Report

### What we achieved this week

#### First Concept

We brainstormed on the rough design and came up with a solution that should be feasible on the technical side. We then refined our idea to a more user friendly and convenient concept. We drew some first sketches on what the device could look like and then created storyboards with a short description of the use cases explaining the functionality. We also wrote down the requirements.

#### Sketches

Sketch

Storyboard1

Storyboard2

#### Requirements

- The target group is
  - device user: people participating in video conferences, in possession of a smartphone or tablet
  - remote user: people participating in video conferences, in possession of a laptop or desktop computer
- The device can hold a smartphone or a tablet and use its camera for the video call
- The device has motors for the movement of the wheels and the device
- The device can be controlled by another person in the video call with their keyboard using the up-, down-, right- and left-arrow keys
- The device uses (in the automatic mode) face tracking to follow the person on the screen 
- The device moves fast and precise enough
- The device is battery-powered

#### Sample the world
We collected pictures from the real world related to our topic. The smartphone holder and wheels are objects that can be combined for our device. The office conference and kitchen are scenarios in which our device could be helpful.

##### Smartphone holder

Smartphone holder

##### Wheels

Wheels

Wheels

##### Office Conference Scenario: One participant is only partly visible

Office

##### Kitchen scenario: Videocall

Kitchen

### What we could not achieve this week

Nothing. 

### What we plan to do for the coming week

We want to evaluate if our ideas are appropriate. We also want to work on the paper prototype, write a component list and think of milestones.

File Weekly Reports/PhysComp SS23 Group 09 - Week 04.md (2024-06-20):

# PhysComp SS23 Group 09 - Week 04

## Progress Report

### What we achieved this week

We created a first paper prototype in class using cardboards, hot glue and plastic cups. (Considering our first sketch and idea of the device). The device can hold a tablet with its triangular form and move its viewing angle with the two wheels. We did not include any buttons yet, because our initial sketch and idea didn't yet consider them really.  

#### First Physical Prototype

Prototype

Prototype Sideview

During the process, we had the idea of using 2 different colored LEDs to signal the user whether the device is currently connected. So we made some changes to the sketch and adapted the prototype a little. We chose indirect light from below the device so that it is both subtle but also able to immediately notify of a problem by changing the color.

#### Updated Sketch 

Sketch Connection

Prototype connected

Prototype notConnected

Initially, we considered incorporating a button or switch on the right side of our device to enable power on and off functionality. However, we eventually opted to design the device to automatically turn on once a tablet or smartphone gets placed into it and turn off as soon as it is removed. Here is a small sketch:

Sketch PowerOn

Next, we also thought about the multimodality of our device and how we can process more physical input. We came up with the idea to give the user the possibility to switch between 3 different modes of operation:  

* Do nothing. Act as a tablet holder.
* Automatically rotate to follow the person's face that is currently in the video. Does nothing if multiple faces are in the video.
* Be remotely controlled by a participant who is not locally present. This requires the remote participant to log on to the device with a password.

These modes can be selected with the according button on the front bottom side of the device. A white LED (that is ideally built into the button) will signal the currently selected active mode.  

Sketch Modi

### Norman's Design Principles

1. Visibility:
   The triangular form and the slightly tilted board on the front of the device make it easy to understand that a phone/tablet has to be placed here. It resembles the shape of an ordinary book/tablet holder.
   The buttons for the 3 modes are also well visible. With descriptions above them, it should be obvious what they do.

2. Feedback:  
   The LEDs on the bottom give feedback of the current connection status and also signal whether the device is powered on. The LEDs in the front panel indicate the current operation mode.

3. Constraints: It is not possible to accidentally turn off the device (and therefore cut any connection) by pushing the wrong button. Likewise, it is not possible to turn off the device when removing the tablet, preserving battery life. Since tablets usually automatically rotate the image so that it is always correctly oriented, it is not even possible to place the tablet incorrectly into the device. Since the front panel buttons simply change the operation mode, it is not possible to do something wrong with them.

4. Mapping: 
   The buttons for the 3 different modes are all next to each other, well-labeled and at a reasonable position.  

5. Consistency:  
   The green light for connection and red light for no connection are consistent with the general understanding of those two colors. A little button on the front indicates that the respective mode is active.

6. Affordance: People are used to putting a book or tablet into a holder or are at least familiar with the concept. Also, people are used to the fact that things happen to the thing they interact with. In our case, the front panel button that is pressed will light up and the respective operation mode will be active. It would be unusual if a light somewhere else were to change. This is similar to our consistent mapping.

### Components List

* Raspberry Pi or Arduino if the RPi cannot be powered with batteries
* MicroSD card for the RPi
* Batteries (e.g. 9V) and power adapter
* Omni Wheel Base
* Three red and three green LEDs OR Three RGB LEDs or a strip
* Three Push-buttons with integrated white LEDs OR additional white LEDs
* A suitable switch that requires little force so that it can act as the main power switch
* Jumper wires
* Breadboard
* Resistors
* Wood or plastic pieces for the case and tablet holder
* Maybe 3D-printed parts

### What we could not achieve this week
We have not fully fleshed out the design of the button panel. Also, we have to find out about the capabilities of the omni wheel base that Matthias mentioned.

### What we plan to do for the coming week

We want to have a look at the omni wheel base from the class inventory. It might be a better solution for the mobility requirements of our device. Then, we can update the sketches and perhaps the paper prototype so they can be presented to the class.

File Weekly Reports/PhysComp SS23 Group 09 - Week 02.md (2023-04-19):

# PhysComp SS23 Group 09 - Week 02

## Progress Report

### What we achieved this week

In class, we learned about sketching and prototypes. Later, we completed the electronics and programming lessons from part 1 of the CTC GO! course. This includes basic battery-powered circuits for driving an LED with resistors and switches. We also programmed the Arduino microcontroller to blink two LEDs at the same time. We than modified the code to make the LEDs blink alternatingly.

We were given the topic _Telepresence System_.

Afterwards, we went through the chapters 1-3 from the Physical Computing Website by NYU as well as the CTC GO! course material.



### What we could not achieve this week

Nothing.

### What we plan to do for the coming week

Elaborate the concept for our project and create sketches.

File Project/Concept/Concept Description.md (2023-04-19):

# Telepresence System Concept

## General Idea

* Remote controlled tablet/Smartphone holder on motorized wheels
* For video conferences where where camera movement/panning is required, e.g. if there are multiple participants in one room or if a single participant is moving around
* Operated by an other participant who is not present
* Automated following of the face of a person who is currently in the frame (none if multiple faces are in the frame)

## See our sketches for further details

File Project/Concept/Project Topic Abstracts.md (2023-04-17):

# PhysComp SS23 Group 09 - Project Topic Abstracts

## Preference 1

### The physics of time

For this topic, we propose a timer that forces students to respond to it, e.g. for finishing a presentation in time. This device can also be used as an alarm clock. On the physical side, the device has some way of notifying that the time is almost up. There should be at least a speaker or buzzer for making a noise. Additionally, one or multiple LEDs could visually indicate the remaining time. Also, the device should have the form of a smartphone holder. In order to force the user to respond to it, the smartphone gets ejected via a motor-controlled spring mechanism when the time is up. This way, students are forced to finish their presentations or get out of bed in time, because they have to catch their smartphone. For convenience, the timer should automatically activate when the smartphone gets placed in the holder. On the computing side, the operation mode (timer or alarm clock) as well as the time can comfortably be set via a smartphone (web app).

There are probably not many people interested in having their smartphone taken hostage and risking to damage it. However, this project can function as a piece of art, highlighting people's dependence on their smartphone. Also, the general concept can be applied to less fragile objects. For example, by launching a ball every hour. If the ball is aimed away from you, you would have to get up from your desk, resulting in a healthy break.

This project fulfills all requirements: It has interaction in both ways, is multimodal, has a physical and computational side and displays the remaining time.

A simple protoype can be created from a few pieces of wood and a spring. There are only a few electronical components required: A computer featuring GPIO and WiFi, e.g. the Raspberry Pi, a motor, a buzzer/speaker, a breadboard, jumper wires, LEDs, resistors and transistors or optocouplers.

## Preference 2

### Telepresence system

The target group for the telepresence device is professionals who attend hybrid meetings, where some participants are physically present in the meeting room, and others join remotely. The device is particularly useful for remote participants who need to actively engage in the meeting but cannot be physically present and enables them to participate as if they were present in the meeting room. Of course the device can also be used outside of the meeting room for any kind of videochat, personal use or similar activities.

The device should be able to rotate automatically look at interesting regions, such as following a person's face while not making too much noise. It should also be able to hold various sizes of tablets or phones securely in place. Additionally, it should have features such as audio and video capabilities.
It should be easy to set up and use and adaptable to different meeting spaces.
The device should be compact and easy to transport so that it fits on a table or desk and blends in with the meeting space. 

The device would require a motorized base that can rotate to follow the remote user's movements. It would also require a tablet or phone holder that can be adjusted to hold various sizes of devices securely. The device would need to be powered by a (rechargeable) battery, and it should be controlled using a mobile app or a web-based interface. The audio and video quality would depend on the tablet or phone's camera and microphone.

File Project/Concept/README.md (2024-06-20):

# Concept

Here you can find our concept description and concept files as well as the CAD model of our front panel and the drawing of our wood parts that we gave to engineering services. You can also find our final presentation here ([PDF](PhysComp_SS23_Final_Presentation.pdf) and [PPTX](PhysComp_SS23_Group_09_Final_Presentation.pptx) with included videos!).

Wood Drawing

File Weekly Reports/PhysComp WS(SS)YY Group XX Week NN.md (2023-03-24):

# PhysComp WS/SS\<YY\> Group \<XX\> - Week \<NN\>

## Progress Report

### What we achieved this week

What goals did you reach this week? What progress did you make in your project? Add pictures, screenshots, or videos of
the things you did (`Weekly Reports/Figures`). Include media inline in Markdown when possible:

A sample picture

### What we could not achieve this week

It's no shame talking about what you could not achieve. Why did you fail to miss your goals? How would you do it
different next time?

### What we plan to do for the coming week

Make a plan what you want to do until the next assignment.

## Add sections as you see fit for the assignment

Some weekly assignments contain other tasks like creating a order list. You can create the subsections as you see fit 
for the assignment.

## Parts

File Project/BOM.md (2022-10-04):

# PhysComp SS|WS\<YY\> - \<Project Title\>

List all necessary electronical and mechanical components that are necessary to assemble your project.

## Bill of materials (BOM)

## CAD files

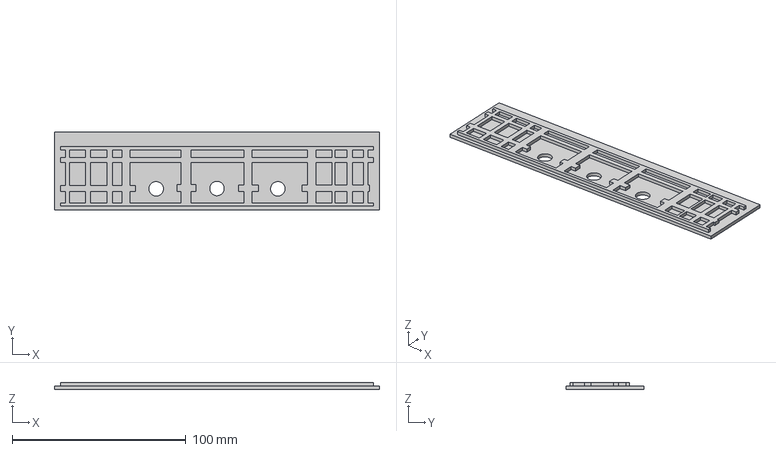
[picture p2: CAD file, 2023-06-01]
Project/Concept/Frontpanel.step
187.0 x 45.0 x 4.00 mm

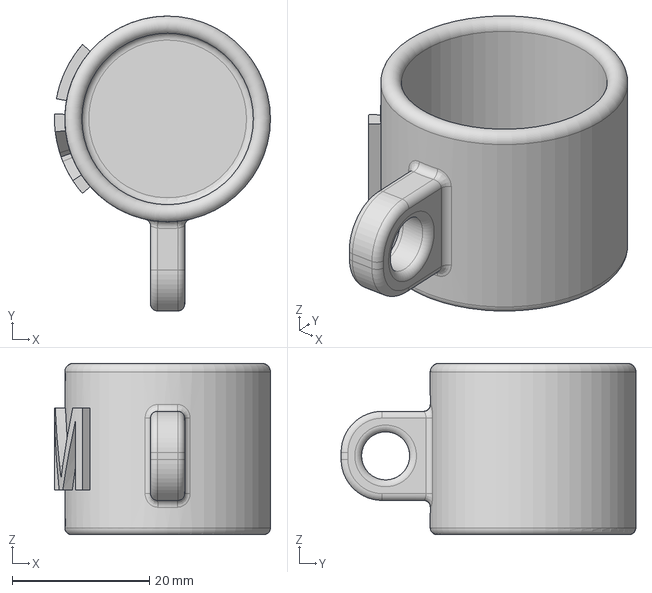
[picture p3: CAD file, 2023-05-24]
Project/Concept/Cup.step
31.5 x 43.0 x 25.0 mm

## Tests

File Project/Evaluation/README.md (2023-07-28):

# Evaluation

Here you can find the original interview notes and our consent letter. For the survey questions we used Google Forms. You can see the documents and results here and in the corresponding progress reports. (Week 11 & 12).

##### Survey Questions:
[PreTest](https://forms.gle/7fHeX9pG4ZDJYAom8)  
[PostTest](https://forms.gle/rbUKTCKbLyy1wq2N8)  

##### Evaluation Results:
[PreTest Results](https://docs.google.com/spreadsheets/d/1y2cAJb8nZkoUx43Uvm1FCK_O2ZUDITeJP3uC_UE-zeA/edit?usp=sharing)  
[PostTest Results](https://docs.google.com/spreadsheets/d/1XBZU3nNgJDz5ueN-R5rub-CaMhOsNVy-h-0skV559PA/edit?usp=sharing)

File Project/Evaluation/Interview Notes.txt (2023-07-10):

##############
# Interviews #
##############

Gruppe 1
--------

- Laut
- Kante runterfallen
- Blickwinkel (Verstellung nicht aufgefallen)
- Untere Beleuchtung nicht aufgefallen
- Ruckartige Bewegungen
- Erschreckend
- Vermutlich gut für Vortragend, Professoren, etc.

Grppe 2
-------
- User stellt hochkant auf (unsicher)
- Grün erkannt
- Rad abgefallen

- Winkel nur für kleine Tische geeignet
- Winkelverstellung nicht aufgefallen
- Tablet-Sicherung an der Seite
- Hochkant gestellt, weil das Tablet gerade so da lag
- Vielleicht Hochkant-Stellen verhindern

Gruppe 3
--------
- Ohne Tablet-Hülle besser, weil sich nicht getraut wird, das Tablet stark herunterzudrücken
- Knöpfe drückbar war nicht direkt ersichtlich (für beide)
- Grün aufgefallen
- Winkel ferngesteuert verstellen wäre gut
- Gerät ist zu schnell und ruckartig
- Tablet ist kurzzeitig vom Schalter gefallen -> Reset auf Freeze
- Ein/Ausschalten ist intuitiv
- Web UI: Links/rechts und turn wurde oft vertauscht -> Buttons tauschen?

- Angst, dass es vom Tisch fährt
- Wackelig
- Blickwinkel aus Remote-Perspektive nicht klar (sieht Tischkante nicht)
- Was passiert, wenn mehrere im Bild sind im Follow Modus? Wie fährt es (nur drehen?)
- Das Gerät ist etwas unhandlich (nicht klappbar)
- Tracking zu spät, Drehung zu abrupt
- Button-Beschriftungen und Farbgebung gut, auch unter dem Gerät (anfangs nicht ganz klar, aber mit Änderung ersichtlich)

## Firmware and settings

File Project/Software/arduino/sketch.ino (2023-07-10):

#include <Adafruit_MotorShield.h>

Adafruit_MotorShield AFMS = Adafruit_MotorShield();
Adafruit_DCMotor *m1 = AFMS.getMotor(1);
Adafruit_DCMotor *m2 = AFMS.getMotor(2);
Adafruit_DCMotor *m3 = AFMS.getMotor(3);
Adafruit_DCMotor *m4 = AFMS.getMotor(4);

void setup() {
    Serial.begin(115200);
    AFMS.begin();
}
 
void loop() {
    if (Serial.available() >= 3) {
        byte axis = Serial.read();
        byte direction = Serial.read();
        byte speed = Serial.read();
        switch (axis) {
          case 0:
            driveY(direction, speed);
            break;
          case 1:
            driveX(direction, speed);
            break;
          case 2:
            rotate(direction, speed);
            break;
        }
    }
}

void setSpeed(byte speed) {
  m1->setSpeed((speed / 6) * 5);
  m2->setSpeed((speed / 6) * 5);
  m3->setSpeed(speed);
  m4->setSpeed((speed / 6) * 5);
}

void driveY(byte direction, byte speed) {

  byte forward = direction == 1 ? FORWARD : BACKWARD;
  byte backward = direction == 1 ? BACKWARD : FORWARD;
  
  m1->run(forward);
  m2->run(forward);
  m3->run(backward);
  m4->run(backward);
  setSpeed(speed);
}

void driveX(byte direction, byte speed) {
  byte forward = direction == 1 ? FORWARD : BACKWARD;
  byte backward = direction == 1 ? BACKWARD : FORWARD;
  
  m1->run(forward);
  m2->run(backward);
  m3->run(backward);
  m4->run(forward);
  setSpeed(speed);
}

void rotate(byte direction, byte speed) {
  byte forward = direction == 1 ? FORWARD : BACKWARD;
  byte backward = direction == 1 ? BACKWARD : FORWARD;
  
  m1->run(backward);
  m2->run(forward);
  m3->run(backward);
  m4->run(forward);
  setSpeed(speed);
}

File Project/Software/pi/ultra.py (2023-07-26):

import RPi.GPIO as GPIO
import time
 
#GPIO Modus (BOARD / BCM)
GPIO.setmode(GPIO.BCM)
 
#GPIO Pins zuweisen
GPIO_TRIGGER = 18
GPIO_ECHO = 24
 
#Richtung der GPIO-Pins festlegen (IN / OUT)
GPIO.setup(GPIO_TRIGGER, GPIO.OUT)
GPIO.setup(GPIO_ECHO, GPIO.IN)
 
def distanz():
    # setze Trigger auf HIGH
    GPIO.output(GPIO_TRIGGER, True)
 
    # setze Trigger nach 0.01ms aus LOW
    time.sleep(0.00001)
    GPIO.output(GPIO_TRIGGER, False)
 
    StartZeit = time.time()
    StopZeit = time.time()
 
    # speichere Startzeit
    while GPIO.input(GPIO_ECHO) == 0:
        StartZeit = time.time()
 
    # speichere Ankunftszeit
    while GPIO.input(GPIO_ECHO) == 1:
        StopZeit = time.time()
 
    # Zeit Differenz zwischen Start und Ankunft
    TimeElapsed = StopZeit - StartZeit
    # mit der Schallgeschwindigkeit (34300 cm/s) multiplizieren
    # und durch 2 teilen, da hin und zurueck
    distanz = (TimeElapsed * 34300) / 2
 
    return distanz
 
if __name__ == '__main__':
    try:
        while True:
            abstand = distanz()
            print ("Gemessene Entfernung = %.1f cm" % abstand)
            time.sleep(0.1)
 
        # Beim Abbruch durch STRG+C resetten
    except KeyboardInterrupt:
        print("Messung vom User gestoppt")
        GPIO.cleanup()

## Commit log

2022-10-04 Create sample weekly report
2023-04-19 Added blinking LEDs GIF
2023-05-02 adding wheel 2
2023-05-24 Added cup
    [Cup.step]
2023-06-01 Added frontpanel STEP
    [Frontpanel.step]
2023-06-01 Added button measuring photo
2023-06-14 Update 2 files
    - /Weekly Reports/Figures/motorTest.gif
    - /Weekly Reports/PhysComp SS23 Group 09 - Week 09.md
2023-06-14 Update file motorTest.gif
2023-07-10 arduino code update
2023-07-10 Update 21 files
    - /Weekly Reports/Figures/evaluation.mp4
    - /Weekly Reports/Figures/evaluation_surveys.jpg
    - /Weekly Reports/Figures/evaluation_pre_setup.jpg
    - /Weekly Reports/Figures/Pretest/_How important is it for you to actively engage and contribute during remote meetings.png
    - /Weekly Reports/Figures/Pretest/_How familiar are you with telepresence devices or similar technologies_Please rate your familiarity.png
    - /Weekly Reports/Figures/Pretest/_How challenging do you find it to actively engage in remote meetings.png
    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
2023-07-19 Added ultrasonic sensor case photos
2023-07-26 Added ultrasonic sensor output
2023-07-28 Added ultrasonic schematic
